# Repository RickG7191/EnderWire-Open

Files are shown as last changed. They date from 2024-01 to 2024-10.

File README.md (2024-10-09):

# EnderWire-Open
This is another option for converting an Ender 3 Pro to a Voron Switchwire. Inspiration for this conversion came from the excellent work of others including [DaRk_dOg](https://github.com/boubounokefalos/Ender_SW/tree/main) and [Steve](https://github.com/stvptrsn).  
  
It is hoped that the 3D printing community will find some value in this work.
  
## Description
One of the key differences that sets this conversion apart from others is that it provides full use of the stock Ender 3 bed size (235x235). The cost of getting that little extra amount involves replacing the top and bottom frame cross members as well as the gantry extrusion with longer versions. One of the replaced 2020 extrusions can be reused as a forward cross member providing better support for the 4040 Y-Axis extrusion, thus it doesn't teeter on the single cross member making frame alignment a bit easier.  

### No Enclosure
This version of the conversion is called "EnderWire-Open" because it does <ins>not</ins> include provisions for an enclosure. For those wanting to print mostly PLA, this is fine as it offers a smaller footprint when not in use. Adaptation to an enclosed version is feasible using longer frame extensions and stretching the side skirts, however I have not endeavored to do so.

### Features
Features of this conversion include:
- Build volume of 235 x 235 x 210
- Optional 6mm or 9mm Y-belt
- Optional smooth idlers or toothed idlers for XY belts
- Optional left endstop, right endstop, or no endstop X-carriage
- XY motor mounts, idler blocks, and gantry blocks optimized for v-slot extrusion
- Shorter Clockwork 2 cable chain mount
- Front skirt option for Mini12864 display or no display
- Front skirt option for hexagon mesh
- Front skirt option to illuminate endcaps with Neopixels or use colored inlay
- Back skirt case fan mount that doesn't use tape (requires gluing 4 small tabs to skirt frame)
- Back skirt standard keystone jacks
- Optional servo actuated Z-probe dock with optional position sensor switches, deck mounted

### Advanced Builder Features
For advanced builders, the following optional features are available:
- Below deck Key-Bak assembly with tension adjustment - [Key-Bak Details](Key-Bak-Details.md)
- Lightened stock bed plate plus alternate Y-carriage
- Custom Z-endstop switch and bracket
- See Build Notes below.

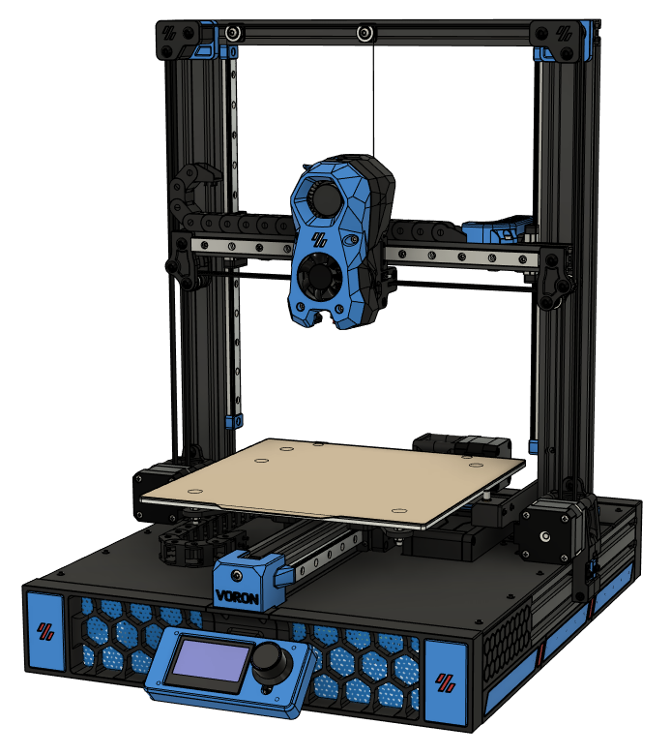
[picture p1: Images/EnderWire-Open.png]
EnderWire Open

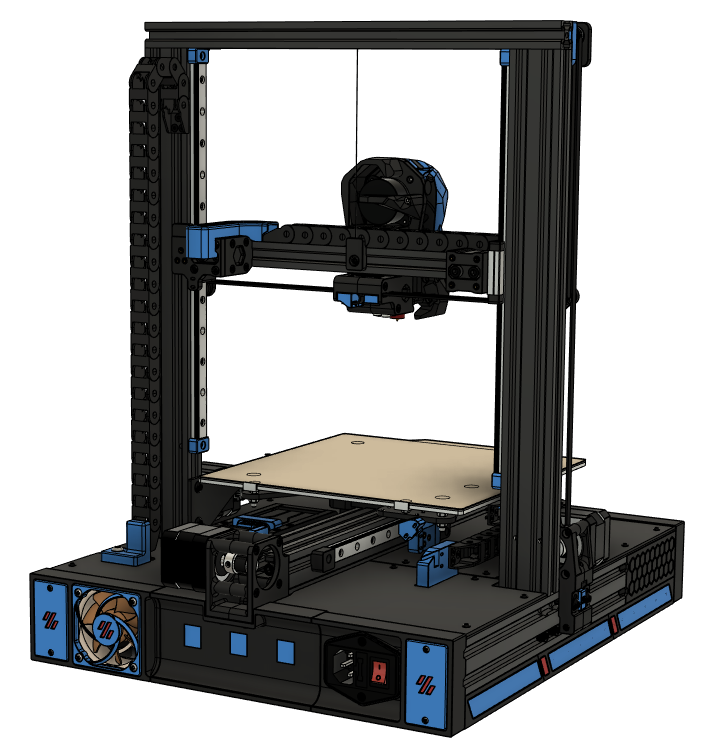
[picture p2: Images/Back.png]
Back View


## Files

### CAD
Complete Fusion 360 files are included in the initial release. Beware, there a upwards of 100 files in the Fusion 360 Archive (.f3z).  
A complete STEP file is included in the CAD folder.

### STLs
STL files for all components except Stealthburner and Mini12864 are included ini the STL folder.

## Bill of Materials
[BOM by Component](BOM-By-Component.md)

## Build Notes
- See [Frame and Gantry Details](Frame-Gantry-Details.md) for information on frame alterations plus gantry idler and belt details.
- The feet are from [Amazon](https://www.amazon.com/gp/product/B00S47D52G/ref=ppx_yo_dt_b_search_asin_title?ie=UTF8&psc=1)
- The Key-Bak assembly uses the spring and 36" Kevlar cord from the regular [13oz Key-Bak](https://www.amazon.com/dp/B0088MQA10?psc=1&ref=ppx_yo2ov_dt_b_product_details)
- The servo used for the Z-probe dock is a TowerPro MG92B from [Adafruit](https://www.adafruit.com/product/2307). I believe an MG90s will also work.
- A modified version of the PCB Klicky probe body and dock are used. The probe has a guard plate that assists with clean docking. The guard plate fits 0.25in x 0.125in countersunk magnets rather than the spec 6mm x 3mm. This is the size I recieved with the kits I purchased. The guard just press fits around the magnets. Glue may be needed.
- The custom z-endstop currently requires a custom PCB to mount the microswitch. Additionally, the support arm for the z-endstop is fabricated from 3mm FR4 / G10 for stiffness.

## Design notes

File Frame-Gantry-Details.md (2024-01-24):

# Frame and Gantry Details
## Frame and Gantry Alteration and Assembly Details
Alterations of the stock Ender 3 Pro frame and gantry includes:
- Replace 2020 Top Cross Member with new 2020 × 360mm v-slot extrusion
- Replace 4040 Main Cross Member with new 2040 × 280mm v-slot extrusion
- Replace 2020 Gantry with new 2020 × 340mm v-slot extrusion
- Repurpose existing 2020 gantry extrusion as new Forward Cross Member
- Add 40×40×13mm Main Bed Beam Spacer and 20×40×13mm Forward Bed Beam Spacer
- Shift 4040 Bed Beam extrusion 20mm forward

The following frame members are used as-is, with the exception of some drilling and tapping as necessary:
- Left & Right Base Members
- Left & Right Columns
- Bed Beam

Reference [Frame Parts](/Images/Frame-Gantry-Details/Frame-Parts.png) for identification of each frame member.  
Reference [Frame Alterations](/Images/Frame-Gantry-Details/Frame-Alterations.png) for overview of new and modified frame members.  

### Bed Beam Spacers
The Main and Forward Bed Beam Spacers may be cut from unused 4040 and 2040 extrusion respectively. Accurate formation of these parts is important for frame squaring and alignment. Since these are very short pieces to work with, and perhaps somewhat difficult to make, STLs for [Printed Spacers](STL/Frame) are an option.

### Required Drilling & Tapping
Aside from cutting new and repurposed extrusions to length, drilling and tapping is required. Specifically, the following is required. Consider laying out and double checking all dimensions for all members prior to performing any cutting or drilling. The instructions below should be accurate, but things happen. Case in point, the Initial Release of the CAD files (Fusion 360) has an error in the location of the tapped holes for the Forward Bed Beam Spacer.
- New 4040 Main Cross Member
  - Tap two holes on each end with an M5×0.8 tap to connect the Left & Right Base Members with 2-M5 SHCS each side
  - Drill four 5.5mm holes midway along the extrusion for 4-M5 SHCS to attach Bed Beam
  - These holes will be 130mm from each end of the extrusion and separated by 20mm at the midpoint
  - Provide clearance for the M5 SHCS heads in the same way as the stock extrusions (a 9mm drill bit should work)
- New 2020 Top Cross Member
  - Drill two 5.5mm holes at each end to align with tapped holes in Left & Right Column Members (10mm and 30mm from ends)
  - The stock Ender 3 Top Cross Member may be used as a template for drilling
  - Provide clearance for the M5 SHCS heads
  - The new Top Cross Member should look just like the stock one, except longer
- New 2020 Forward Cross Member (repurposed 2020 gantry extrusion)
  - Drill one 5.5mm hole 10mm from each end to align with the lower inside holes of the Left & Right Base Members
  - These holes will be 300mm apart along the 320mm long extrusion
  - Drill two 5.5mm holes midway along the extrusion for 2-M5 SHCS to attach the Bed Beam
  - These holes will be 150mm from each of the extrusion and separated by 20mm at the midpoint
  - Provide clearance for the M5 SHCS heads
- Existing Bed Beam Member
  - Confirm that the extrusion is 350mm in length
  - Locate the four existing tapped holes for mounting the Bed Beam to the existing Main Cross Member
  - Drill two 4.2mm holes spaced 20mm backward of the existing holes (105mm from the back end of the extrusion)
  - Drill two 4.2mm holes spaced 80mm from the front end of the extrusion
  - Tap the four new holes with an M5×0.8 tap
  - Ensure that the lower two holes at the front end of the extrusion are tapped for an M5 bolt to attach the Y-Idler
  - Ensure that the four holes at the back end of the extrusion are tapped for an M5 bolt to attach the Y-Motor
- Main and Forward Bed Beam Spacers
  - If using 4040 and 2040 extrusion for bed beam spacers, drill each hole with a 5.5mm drill to provide clearance for M5 bolts
- Existing Left & Right Base Members
  - Ensure that the ends are tapped for M5 bolts to attach the Forward Cross Member and skirt components
- Gantry
  - Aside from cutting the new 2020 Gantry to length, no drilling or tapping is necessary

### Frame Assembly
Assemble the frame using M5×25 and M5×45 SHCS bolts with washers. With the exception of perhaps two M5×25 bolts for the Forward Cross Member, these bolts come from the Ender 3 Pro frame. Refer to the CAD models for specifics. Square and align the frame in the same manner as other builds described elsewhere.

## Gantry, Idler, and Belt Details
### Gantry
The new longer gantry extrusion provides full use of the MGN12 × 300mm linear rail and thus full use of the 235mm bed width and then some. Two options are provided for the gantry belt idlers: toothed or smooth. The smooth idler option is generally more economical as the Gates GT2 toothed idlers can be pricey. Whichever option is chosen for the gantry, the corresponding option should be used for the upper idlers to maintain belt alignment.

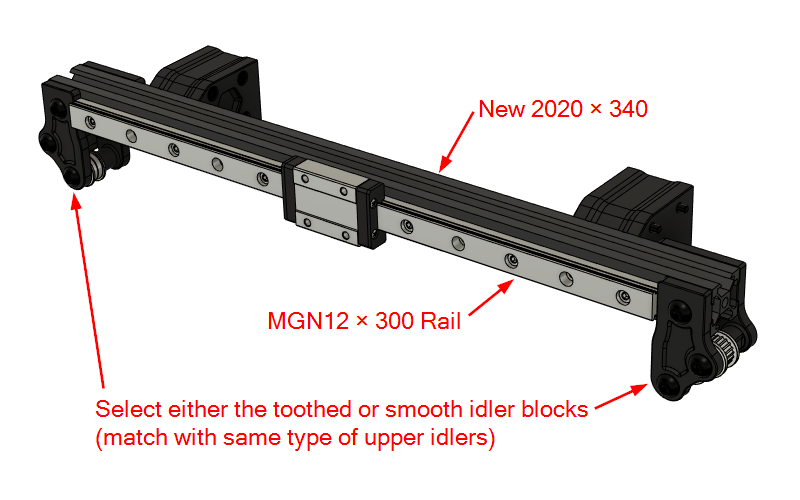
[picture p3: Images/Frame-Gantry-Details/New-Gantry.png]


### Toothed Option
The toothed option requires a total of six toothed idlers, two for the gantry and four for the upper idlers, plus two smooth F695 idler assemblies.

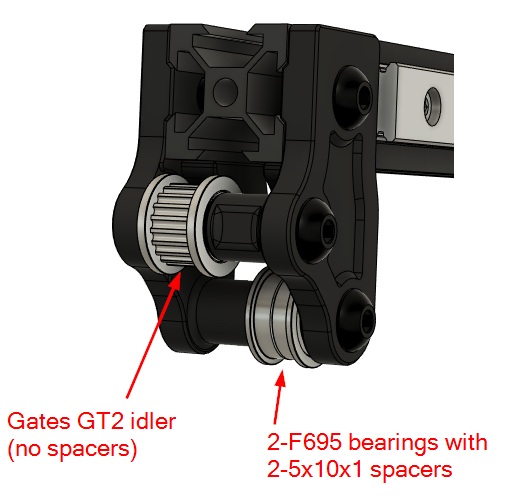
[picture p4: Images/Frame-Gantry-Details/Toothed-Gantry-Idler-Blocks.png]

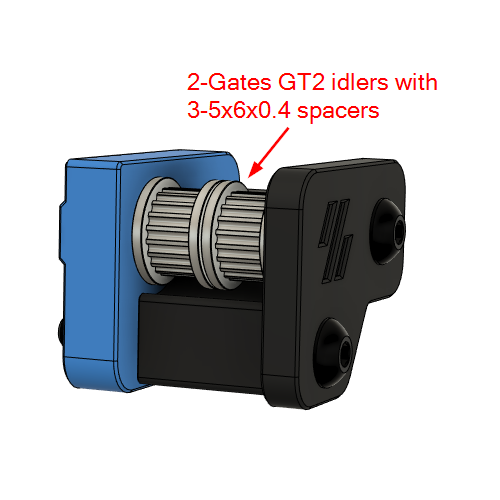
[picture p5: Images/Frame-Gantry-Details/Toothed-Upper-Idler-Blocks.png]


### Smooth Option
The smooth option requires a total of eight F695 idler assemblies.

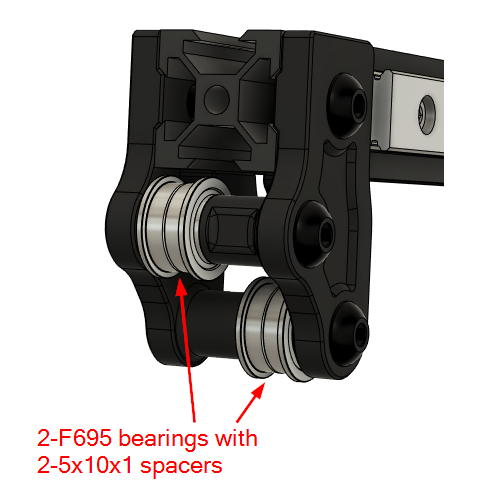
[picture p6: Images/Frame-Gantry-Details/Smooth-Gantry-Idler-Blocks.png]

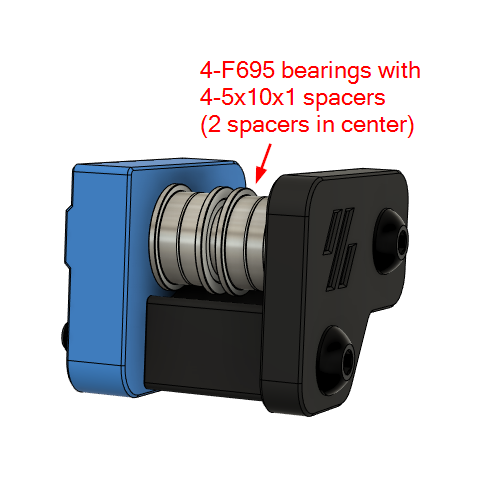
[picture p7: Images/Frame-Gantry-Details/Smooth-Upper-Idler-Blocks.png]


### Belt Details
The Gantry uses Gates 6mm GT2 belting. The spacing and offsets for the XZ belts are identical to Voron Switchwire and the implementation by [DaRk_dOg](https://github.com/boubounokefalos/Ender_SW/tree/main).  
- Belt spacing is 10mm centerline to centerline.
- Centerline of Belt B is 24mm from face of frame.
- Centerline of Belt A is 14mm from face of frame.
- Motor B and Motor A pulley offsets measured from the outside edge of the frame is 10.62mm.

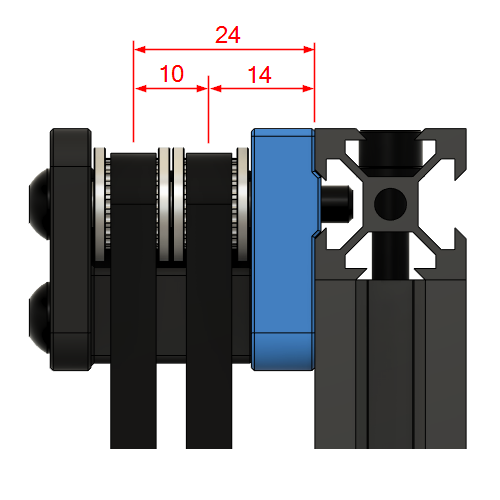
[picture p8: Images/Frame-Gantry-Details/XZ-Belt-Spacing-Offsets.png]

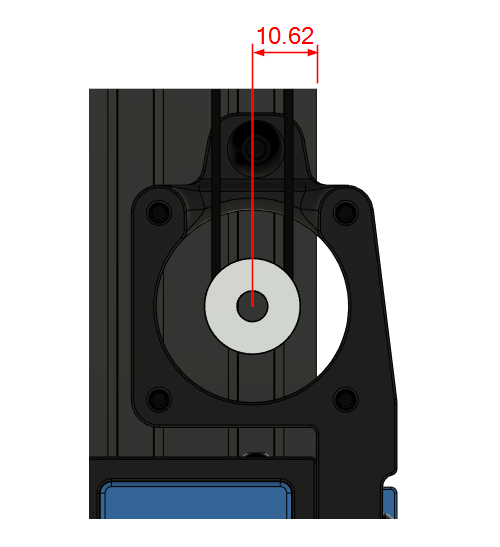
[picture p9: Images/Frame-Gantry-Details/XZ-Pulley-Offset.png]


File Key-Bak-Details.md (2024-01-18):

# Key-Bak Details
The adjustable tension Key-Bak dispenses with the Key-Bak housing and only uses the cord and flat coil spring. As illustrated in the images below, the spring housing meshes with the cord spool in such a way that allows the spring to be wound tighter or looser in order to match the gantry load. In addition to the original intent of the Key-Bak to prevent the grantry from unexpectedly dropping if the XY-motors loose power, it also counterbalances the gantry weight to minimize the differential motor load between upward and downward gantry movements. Note that this sort of adjustment can be accomplished with the unmodified Key-Bak by adjusting the length of the cord. Otherwise, I just wanted the Key-Bak mechanism tucked away under the deck with an easy way to adjust the tension. Personal preference.
## Cord Spool
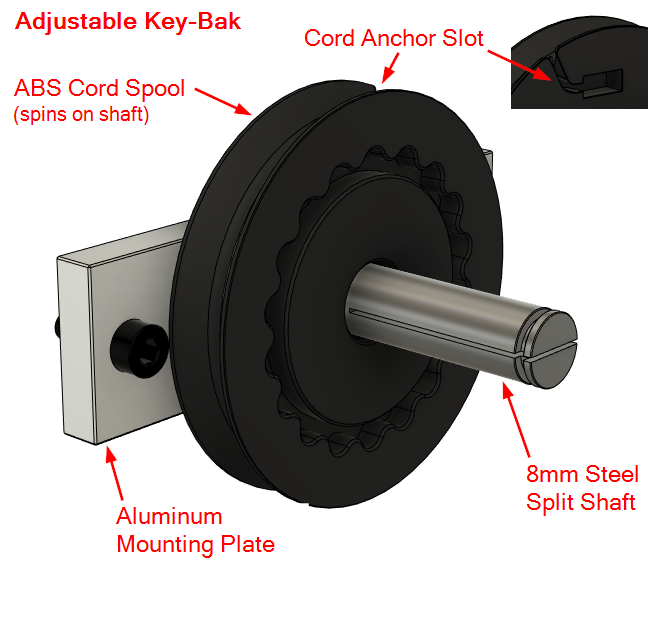
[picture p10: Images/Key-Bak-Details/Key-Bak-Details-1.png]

## Spring Housing
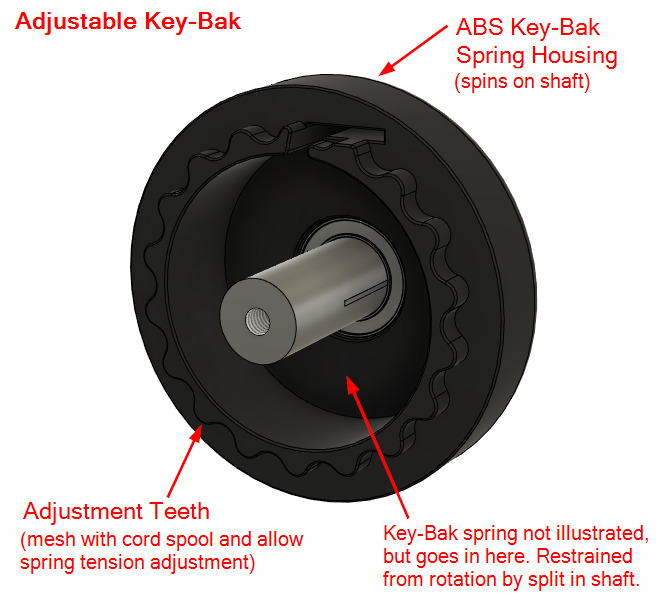
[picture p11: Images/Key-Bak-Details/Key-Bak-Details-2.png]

## Assembled
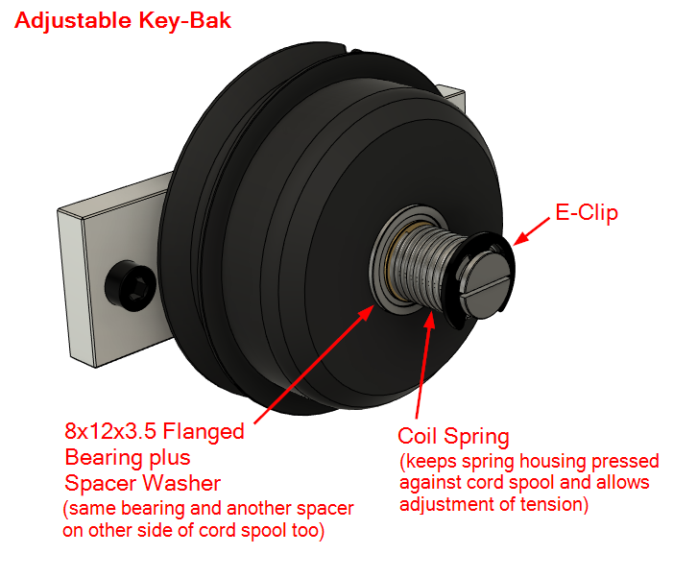
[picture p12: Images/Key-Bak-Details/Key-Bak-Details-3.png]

## Installed
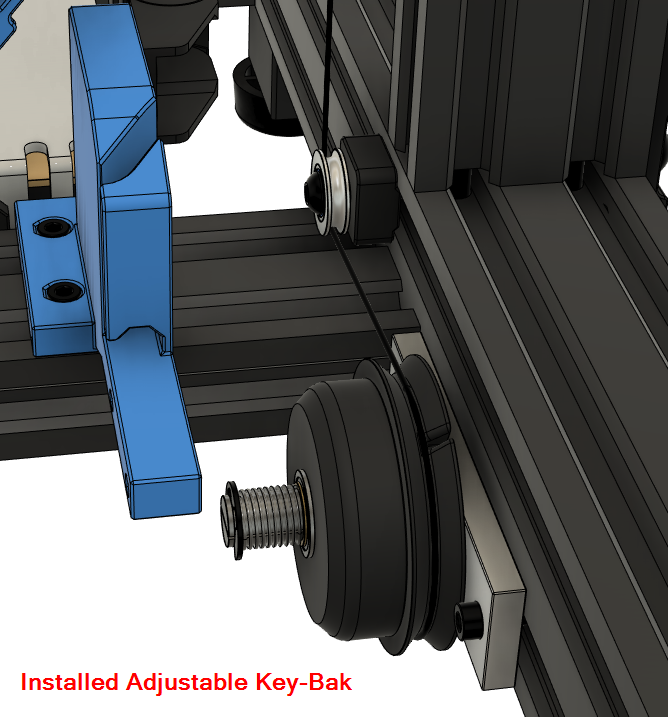
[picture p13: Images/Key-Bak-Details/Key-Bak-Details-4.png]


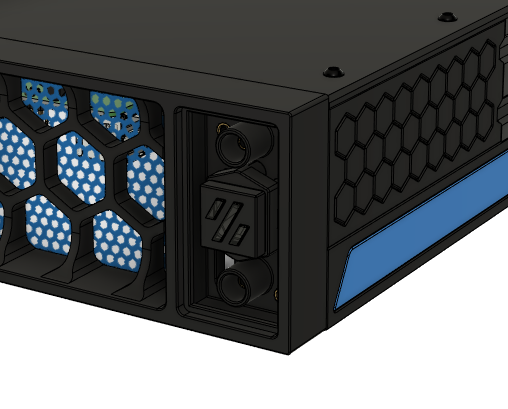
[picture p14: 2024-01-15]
Images/FrontEndcap-Neopixel2.png

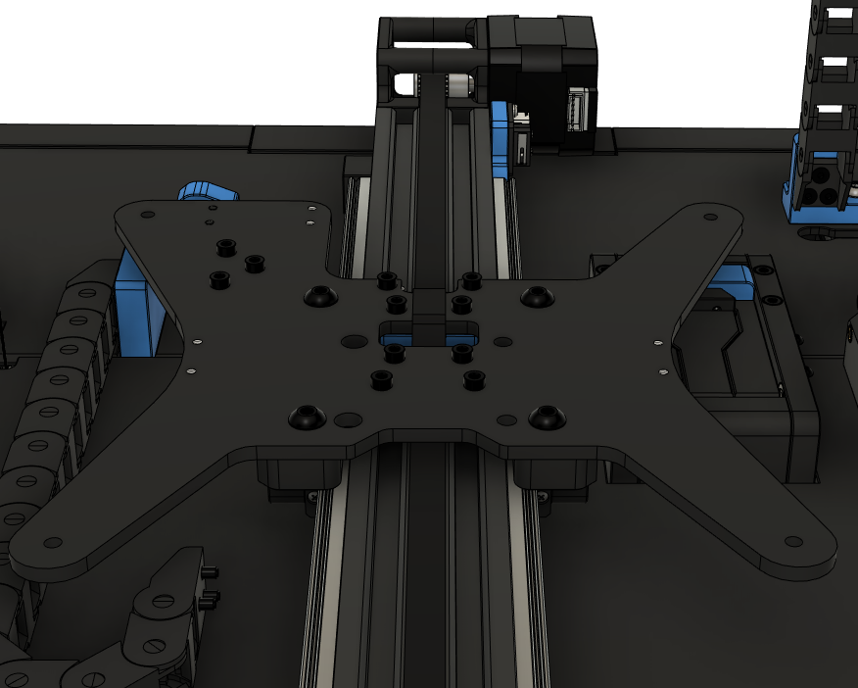
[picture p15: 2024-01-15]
Images/BedPlate.png

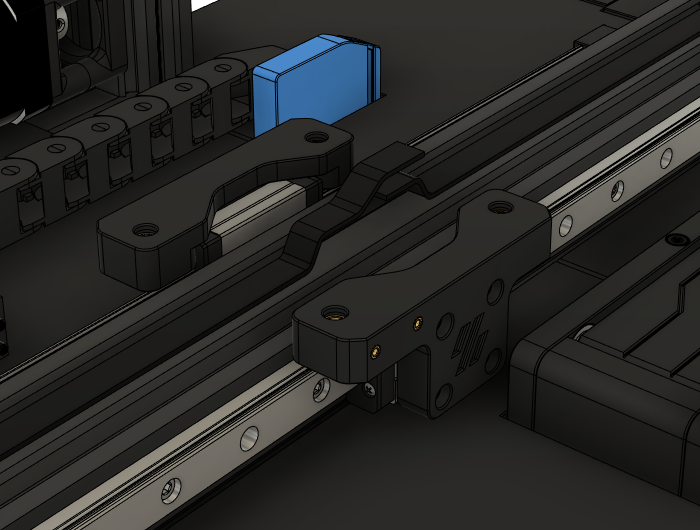
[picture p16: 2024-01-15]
Images/BedCarriage.png

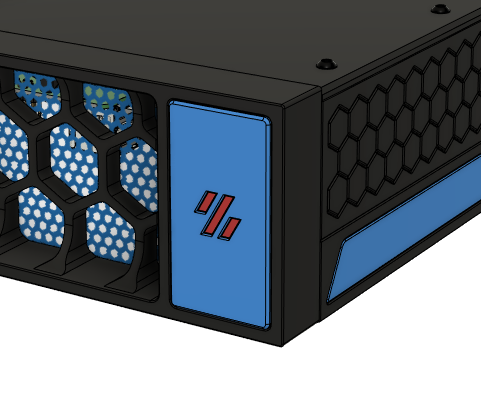
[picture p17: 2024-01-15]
Images/FrontEndcap-Inlay.png

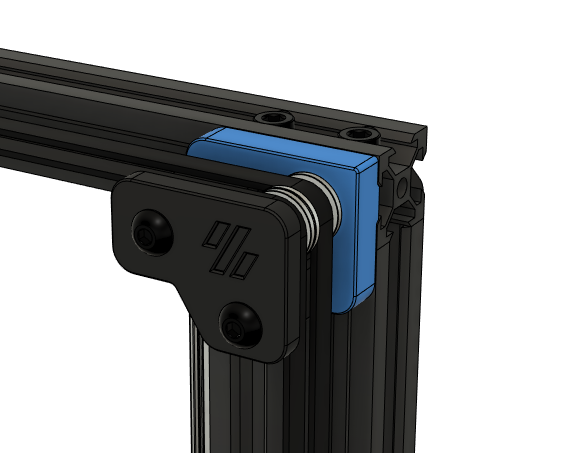
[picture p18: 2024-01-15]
Images/UpperIdlerToothed.png

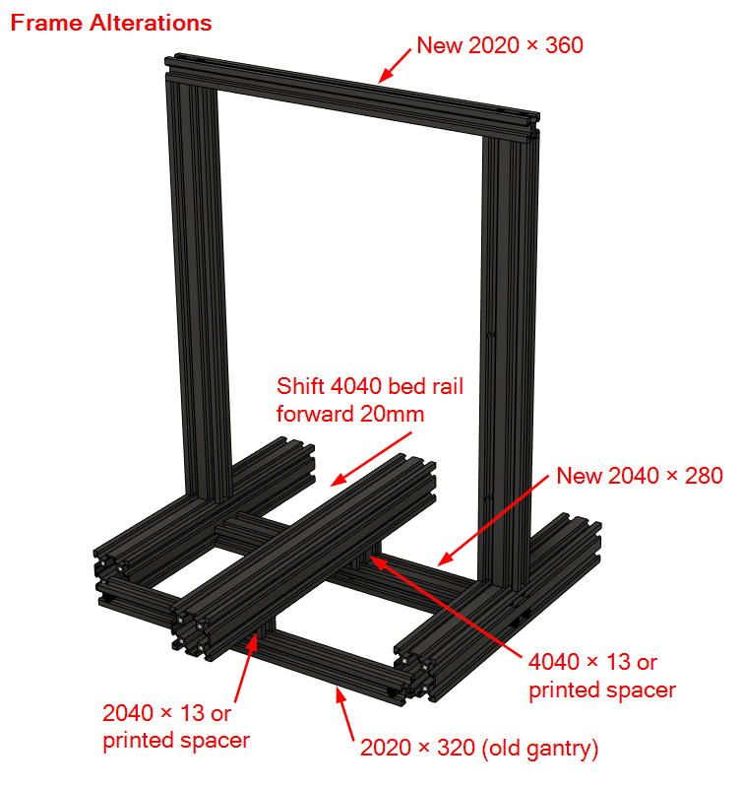
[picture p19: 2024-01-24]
Images/Frame-Gantry-Details/Frame-Alterations.png

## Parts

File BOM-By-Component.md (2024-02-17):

# BOM By Component
Parts and hardware broken down by component. See CAD files for specific details.
<br/><br/>
Items currently not included in this listing:
- Stealthburner toolhead
- Mini12864 display
- Z-Endstop (this currently requires a fiberglass bracket and custom PCB)
- Below deck Key-Bak (this currently requires machined pulleys, machined pin, and aluminum mounting plate)
<br/><br/>

| Component | Count | Part Description | Note |
| :--- | :---: | :--- | :--- |
| Frame | 1 | 2020 × 340 V-Slot Extrusion | Gantry |
| Frame | 1 | 2020 × 360 V-Slot Extrusion | Top Cross Member |
| Frame | 1 | 2040 × 280 V-Slot Extrusion | Main Cross Member |
| Frame | 14 | M5 × 45 SHCS | w/washer |
| Frame | 6 | M5 × 25 SHCS | w/washer |
||
| Linear Rails | 5 | MGN12 × 300 | |
| Linear Rails | 30 | M3 × 8 SHCS | 6 each rail |
| Linear Rails | 30 | M3 T-Nut | 6 each rail |
||
| XZ-Motor Mounts | 2 | 6mm GT2 20T Pulley | |
| XZ-Motor Mounts | 4 | M3 Threaded Insert | |
| XZ-Motor Mounts | 10 | M3 × 30 SHCS | |
| XZ-Motor Mounts | 2 | M3 × 40 SHCS | |
| XZ-Motor Mounts | 2 | M5 × 10 BHCS | |
| XZ-Motor Mounts | 4 | M5 × 16 BHCS | |
| XZ-Motor Mounts | 6 | M5 T-Nut | |
||
| Y-Motor Mount - 9mm Option | 1 | 9mm GT2 20T Pulley | |
| Y-Motor Mount - 9mm Option | 3 | M3 Threaded Insert | |
| Y-Motor Mount - 9mm Option | 1 | M3 × 35 SHCS | |
| Y-Motor Mount - 9mm Option | 4 | M3 × 40 SHCS | |
| Y-Motor Mount - 9mm Option | 2 | M5 × 16 SHCS | |
| Y-Motor Mount - 9mm Option | 2 | M5 × 16 BHCS | |
||
| Y-Motor Mount - 6mm Option | 1 | 6mm GT2 20T Pulley | |
| Y-Motor Mount - 6mm Option | 3 | M3 Threaded Insert | |
| Y-Motor Mount - 6mm Option | 1 | M3 × 35 SHCS | |
| Y-Motor Mount - 6mm Option | 4 | M3 × 40 SHCS | |
| Y-Motor Mount - 6mm Option | 4 | M5 × 16 BHCS | |
||
| Y-Idler - 9mm Option | 1 | 9mm GT2 20T Idler | |
| Y-Idler - 9mm Option | 1 | 5 × 24 Pin | |
| Y-Idler - 9mm Option | 2 | 5 × 7 × 0.5 Spacer | |
| Y-Idler - 9mm Option | 2 | M3 Threaded Insert | |
| Y-Idler - 9mm Option | 1 | M4 Threaded Insert | |
| Y-Idler - 9mm Option | 1 | M4 × 12 BHCS | |
| Y-Idler - 9mm Option | 2 | M5 × 16 BHCS | |
||
| Y-Idler - 6mm Option | 1 | 6mm GT2 20T Idler | |
| Y-Idler - 6mm Option | 1 | 5 × 20 Pin | |
| Y-Idler - 6mm Option | 2 | 5 × 7 × 0.5 Spacer | |
| Y-Idler - 6mm Option | 2 | M3 Threaded Insert | |
| Y-Idler - 6mm Option | 1 | M4 Threaded Insert | |
| Y-Idler - 6mm Option | 1 | M4 × 12 BHCS | |
| Y-Idler - 6mm Option | 2 | M5 × 16 BHCS | |
||
| Bed Carriage | 2 | M2 Threaded Insert | For ADXL |
| Bed Carriage | 4 | M5 Threaded Insert | |
| Bed Carriage | 8 | M3 × 8 SHCS | |
| Bed Carriage | 4 | M5 × 16 BHCS | |
||
| Y-Belt Clamp | 8 | M3 Threaded Insert | |
| Y-Belt Clamp | 8 | M3 × 12 SHCS | |
||
| Y-Chain Mount - Bed | 6 | M3 Threaded Insert | |
| Y-Chain Mount - Bed | 3 | M3 × 12 SHCS | |
| Y-Chain Mount - Bed | 3 | M3 × 6 FHCS | |
| Y-Cable Mount - Bed | 2 | M3 × 8 SHCS | |
||
| Y-Chain Mount - Base | 3 | M3 Threaded Insert | |
| Y-Chain Mount - Base | 2 | M3 × 8 SHCS | |
| Y-Chain Mount - Base | 2 | M3 T-Nut | |
| Y-Chain Mount - Base | 3 | M3 × 6 FHCS | |
||
| Y-Limit Switch | 1 | Creality Endstop PCB | |
| Y-Limit Switch | 2 | M2.5 × 6 STS | |
| Y-Limit Switch | 2 | M3 × 8 SHCS | |
| Y-Limit Switch | 2 | M3 T-Nut | |
||
| Y-Carriage Stop | 1 | M3 × 8 SHCS | |
| Y-Carriage Stop | 1 | M3 T-Nut | |
||
| Z-Carriage Stops | 4 | M3 × 8 SHCS | |
| Z-Carriage Stops | 4 | M3 T-Nut | |
||
| Z-Bearing Blocks | 8 | M3 Threaded Insert | |
| Z-Bearing Blocks | 8 | M3 × 30 SHCS | |
| Z-Bearing Blocks | 4 | M5 × 40 SHCS | |
| Z-Bearing Blocks | 4 | M5 T-Nut | |
||
| Gantry Pulley Blocks - Toothed Option | 2 | 6mm GT2 20T Idler | |
| Gantry Pulley Blocks - Toothed Option | 4 | F695 Bearing | |
| Gantry Pulley Blocks - Toothed Option | 4 | 5 × 10 × 1 Spacer | |
| Gantry Pulley Blocks - Toothed Option | 6 | M5 × 10 BHCS | |
| Gantry Pulley Blocks - Toothed Option | 4 | M5 × 30 BHCS | |
| Gantry Pulley Blocks - Toothed Option | 6 | M5 T-Nut | |
||
| Gantry Pulley Blocks - Smooth Option  | 8 | F695 Bearing | |
| Gantry Pulley Blocks - Smooth Option  | 8 | 5 × 10 × 1 Spacer | |
| Gantry Pulley Blocks - Smooth Option  | 6 | M5 × 10 BHCS | |
| Gantry Pulley Blocks - Smooth Option  | 4 | M5 × 30 BHCS | |
| Gantry Pulley Blocks - Smooth Option  | 6 | M5 T-Nut | |
||
| Upper Idlers - Toothed Option | 4 | 6mm GT2 20T Idler | |
| Upper Idlers - Toothed Option | 2 | 5 × 30 Pin | |
| Upper Idlers - Toothed Option | 6 | 5 × 6 × 0.4 Spacer | |
| Upper Idlers - Toothed Option | 4 | M5 × 40 BHCS | |
| Upper Idlers - Toothed Option | 4 | M5 T-Nut | |
||
| Upper Idlers - Smooth Option | 8 | F695 Bearing | |
| Upper Idlers - Smooth Option | 2 | 5 × 30 Pin | |
| Upper Idlers - Smooth Option | 8 | 5 × 10 × 1 Spacer | |
| Upper Idlers - Smooth Option | 4 | M5 × 40 BHCS | |
| Upper Idlers - Smooth Option | 4 | M5 T-Nut | |
||
| X-Carriage | 12 | M3 Threaded Insert | |
| X-Carriage | 4 | M3 × 8 SHCS | |
| X-Carriage | 6 | M3 × 12 SHCS | |
| X-Carriage | 2 | M3 × 16 SHCS | |
| X-Carriage | 3 | M3 × 40 SHCS | |
| X-Carriage | 3 | M3 Hex Nut | |
| X-Carriage | 1 | Omron D2F-L Switch | Optional X-Endstop  |
| X-Carriage | 2 | M2 × 10 STS | Optional X-Endstop  |
||
| Z-Chain Mount - Gantry | 3 | M3 Threaded Insert | |
| Z-Chain Mount - Gantry | 4 | M3 × 8 BHCS | |
| Z-Chain Mount - Gantry | 3 | M3 × 6 FHCS | |
||
| Z-Chain Mount - Base | 3 | M3 Threaded Insert | |
| Z-Chain Mount - Base | 3 | M3 × 6 FHCS | |
| Z-Chain Mount - Base | 1 | M5 × 16 BHCS | |
| Z-Chain Mount - Base | 1 | M5 T-Nut | |
||
| XZ-Cable Cover | 1 | M3 × 8 SHCS | |
| XZ-Cable Cover | 1 | M3 T-Nut | |
||
| Foot Risers | 4 | M5 × 16 BHCS | |
| Foot Risers | 4 | M5 × 20 BHCS | |
| Foot Risers | 4 | M5 Hex Nut | |
||
| Bottom Panel | 1 | 3 × 352 × 398 Acrylic Panel | |
| Bottom Panel | 4 | M3 × 8 BHCS | |
||
| Bottom Panel Support Brackets | 2 | M3 Threaded Insert | |
| Bottom Panel Support Brackets | 4 | M2 × 10 STS | |
||
| Frame Extensions | 8 | M3 Threaded Insert | |
| Frame Extensions | 8 | M3 × 8 SHCS | |
| Frame Extensions | 4 | M5 × 12 BHCS | |
||
| Front Skirt | 14 | M3 Threaded Insert | |
| Front Skirt | 10 | M3 × 8 SHCS | |
| Front Skirt | 2 | M3 × 16 SHCS | Mini12864 mounting  |
||
| Front Skirt Endcaps | 4 | M3 Threaded Insert | |
| Front Skirt Endcaps | 2 | Neopixel | LED option |
||
| Back Skirt | 4 | M2 Threaded Insert | |
| Back Skirt | 9 | M3 Threaded Insert | |
| Back Skirt | 6 | M3 × 8 SHCS | |
| Back Skirt | 8 | M5 × 12 BHCS | |
||
| Back Skirt Endcaps | 4 | M2 × 6 BHCS | |
||
| Power Inlet | 1 | Ender 3 Power Inlet | |
| Power Inlet | 2 | M3 × 10 FHCS | |
||
| Shock Guard | 1 | M3 × 20 SHCS | |
||
| Case Fan | 1 | 60mm Fan | |
| Case Fan | 4 | M3 Threaded Insert | |
| Case Fan | 4 | M3 × 8 BHCS | |
||
| Fan Deflector | 2 | M3 × 8 SHCS | |
| Fan Deflector | 2 | M3 T-Nut | |
||
| Side Skirts | 2 | M3 Threaded Insert | |
| Side Skirts | 22 | M2.5 × 5 STS | |
| Side Skirts | 22 | M3 × 8 SHCS | |
||
| Power Supply Brackets | 4 | M3 × 8 SHCS | |
| Power Supply Brackets | 4 | M3 T-Nut | |
| Power Supply Brackets | 4 | M4 × 6 BHCS | |
||
| Deck Panels | 18 | M3 × 8 BHCS | |
| Deck Panels | 6 | M3 T-Nut | |
||
| Deck Panel Supports | 8 | M3 Threaded Insert | |
| Deck Panel Supports | 4 | M3 × 20 SHCS | |
||
| Y-Cable Cover | 1 | M3 × 8 SHCS | |
| Y-Cable Cover | 1 | M3 T-Nut | |
||
| DIN Rails | 1 | DIN35 × 200mm | Front |
| DIN Rails | 1 | DIN35 × 160mm | Back |
| DIN Rails | 4 | M5 × 6 BHCS | |
| DIN Rails | 4 | M5 T-Nut | |
||
| XZ-Belts | 2 | 6mm GT2 × 1550mm | Includes 50mm extra |
||
| Y Belt - 9mm Option | 1 | 6mm GT2 × 900mm | Includes 50mm extra |
| Y-Belt - 6mm Option | 1 | 9mm GT2 × 900mm | Includes 50mm extra |
||
| Z-Probe Dock | 1 | TowerPro MG92B Servo | |
| Z-Probe Dock | 2 | F695 Bearing | |
| Z-Probe Dock | 1 | 5 × 50 Pin | |
| Z-Probe Dock | 2 | 5 × 10 × 1 Spacer | |
| Z-Probe Dock | 2 | M2 Threaded Insert | |
| Z-Probe Dock | 2 | M2 × 6 SHCS | Servo mounting |
| Z-Probe Dock | 1 | M2 × 8 SHCS | Link rod |
| Z-Probe Dock | 1 | M2 × 12 SHCS | Link rod |
| Z-Probe Dock | 2 | M2 Washer | Link rod |
| Z-Probe Dock | 1 | M2 Hex Nut | Link rod |
| Z-Probe Dock | 2 | 2 × 3.4 × 3.4 Bushing | Link rod |
| Z-Probe Dock | 5 | M3 Threaded Insert | |
| Z-Probe Dock | 3 | M3 × 12 SHCS | |
| Z-Probe Dock | 1 | M3 × 16 SHCS | |
| Z-Probe Dock | 4 | M3 × 45 SHCS | |
| Z-Probe Dock | 1 | M3 Hex Nut | |
| Z-Probe Dock | 4 | M3 T-Nut | |
| Z-Probe Dock | 2 | Omron D2F-L Switch | Optional |
| Z-Probe Dock | 4 | M2 × 10 STS | Optional |
||
| PCB Klicky Dock | 2 | 6 × 3 Magnets | |
| PCB Klicky Dock | 4 | M2 × 8 STS | |
| PCB Klicky Dock | 2 | M3 × 6 FHCS | |

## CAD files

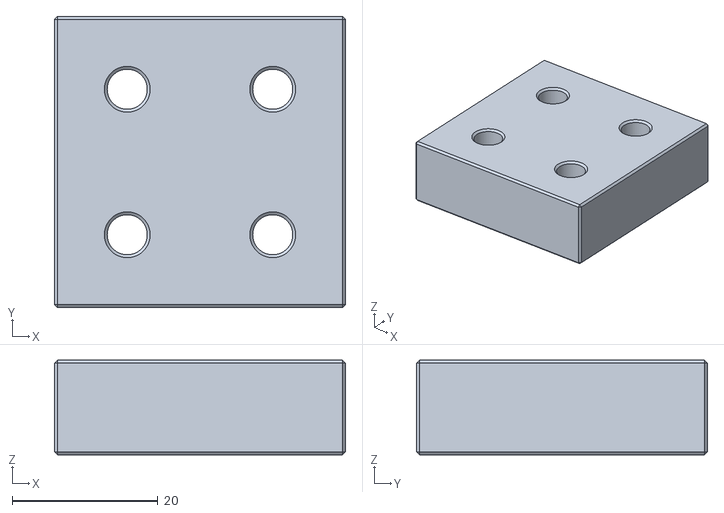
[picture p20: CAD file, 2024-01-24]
STL/Frame/main_bed_beam_spacer.stl
40.0 x 40.0 x 13.0

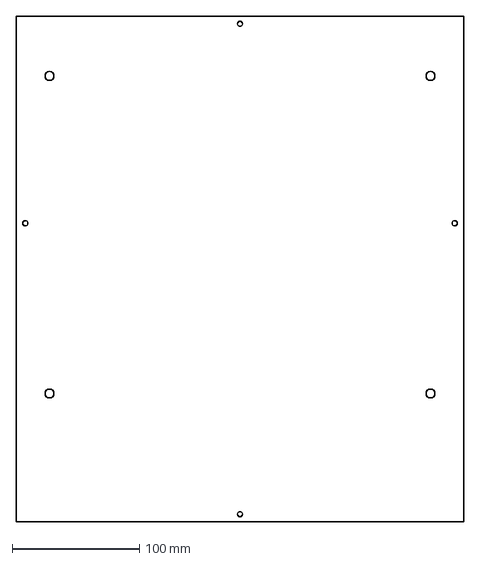
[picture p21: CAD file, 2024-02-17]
DXF/BottomPanel.dxf
352.0 x 398.0 mm

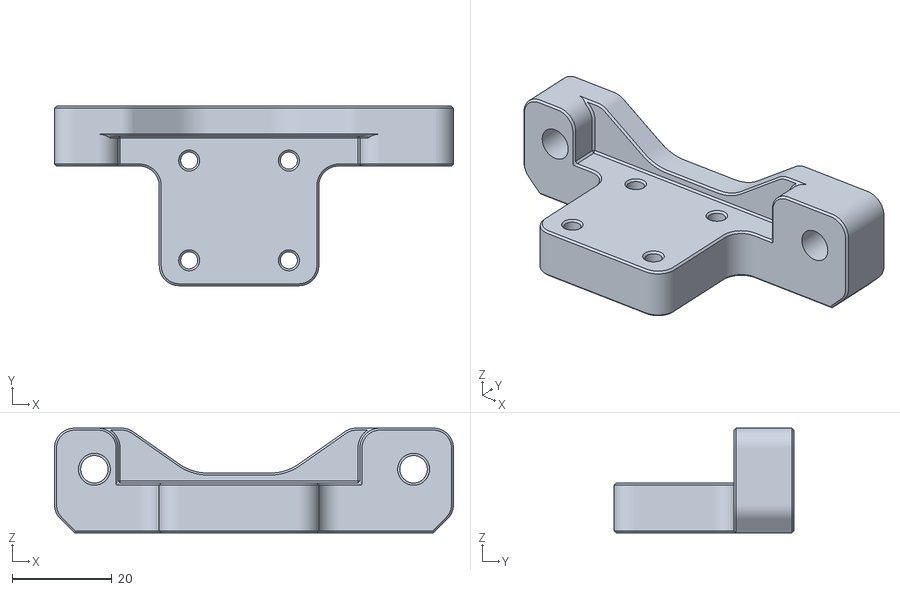
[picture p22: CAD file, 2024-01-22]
STL/Bed/y_axis_bed_carriage_a.stl
80.0 x 36.0 x 21.0

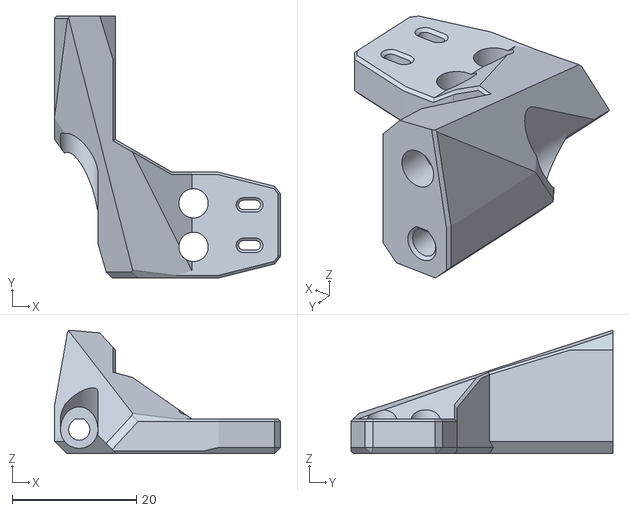
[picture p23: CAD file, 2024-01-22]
STL/Clockwork_2/chain_anchor_3hole_sw_short.stl
36.4 x 42.1 x 19.8

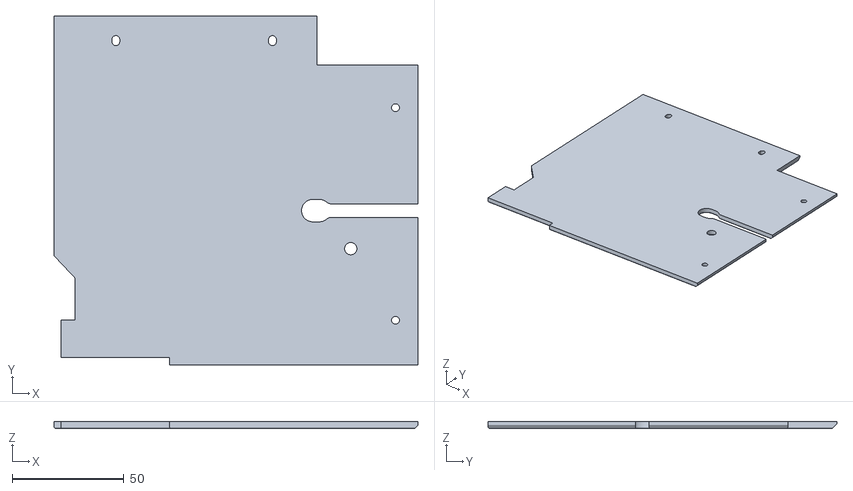
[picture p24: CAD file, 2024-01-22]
STL/Deck/deck_back_right.stl
162.6 x 156.0 x 3.00

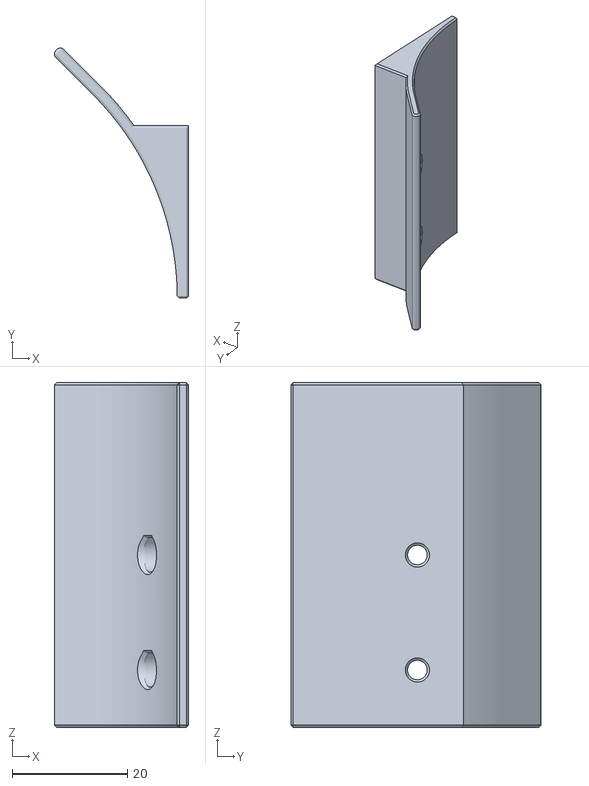
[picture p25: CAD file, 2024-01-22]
STL/Electronics/fan_deflector.stl
23.4 x 43.5 x 60.0

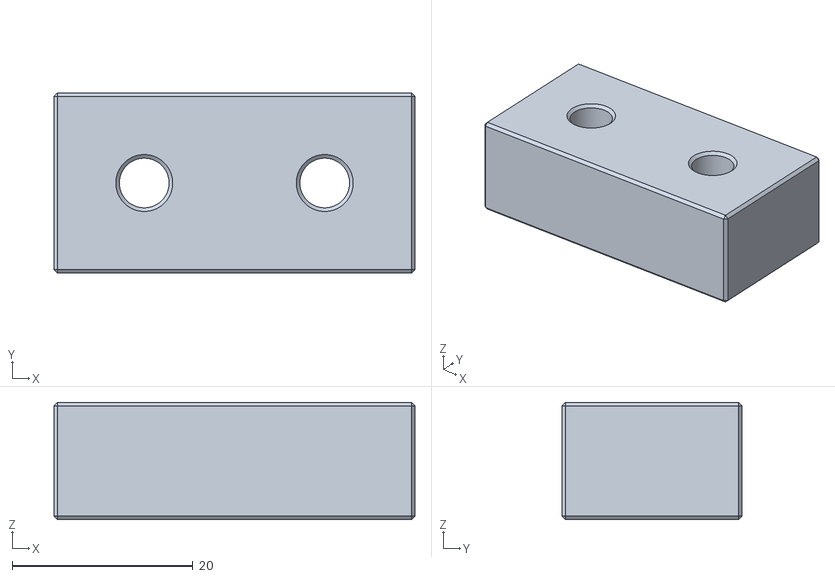
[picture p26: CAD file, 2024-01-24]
STL/Frame/forward_bed_beam_spacer.stl
40.0 x 20.0 x 13.0

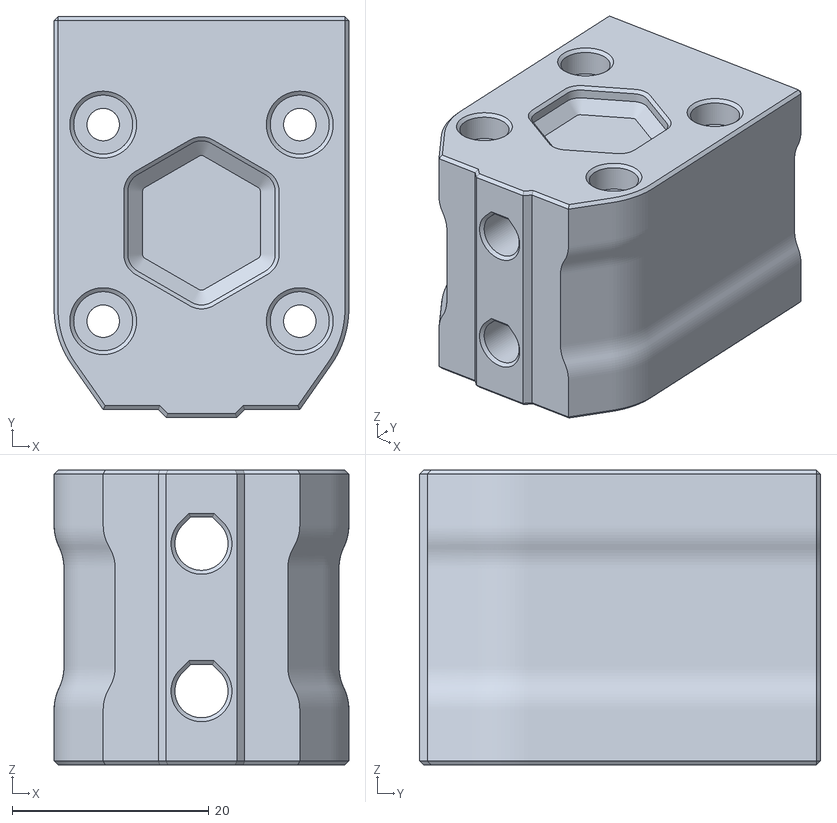
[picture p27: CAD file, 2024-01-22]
STL/Gantry/z_bearing_block_x2.stl
30.0 x 40.8 x 30.0

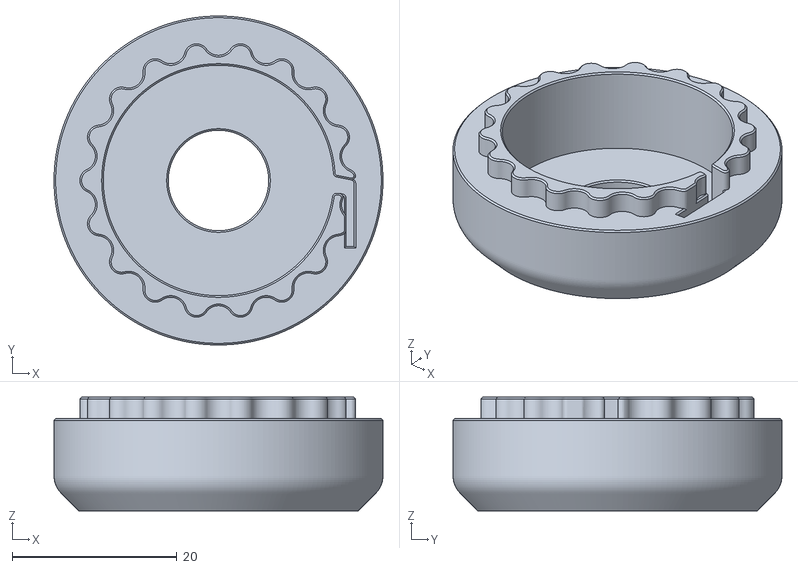
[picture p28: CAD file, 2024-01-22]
STL/KeyBak/keybak_spring_housing.stl
40.0 x 40.0 x 13.8

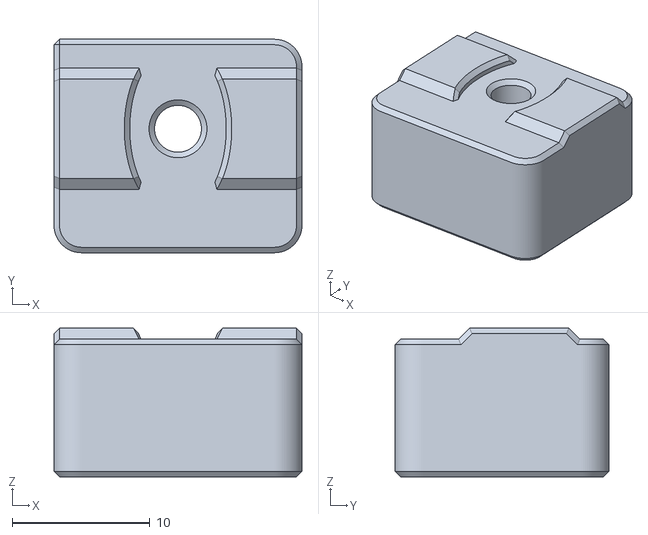
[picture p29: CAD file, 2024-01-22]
STL/Misc/y_carriage_stop.stl
18.0 x 15.5 x 10.8

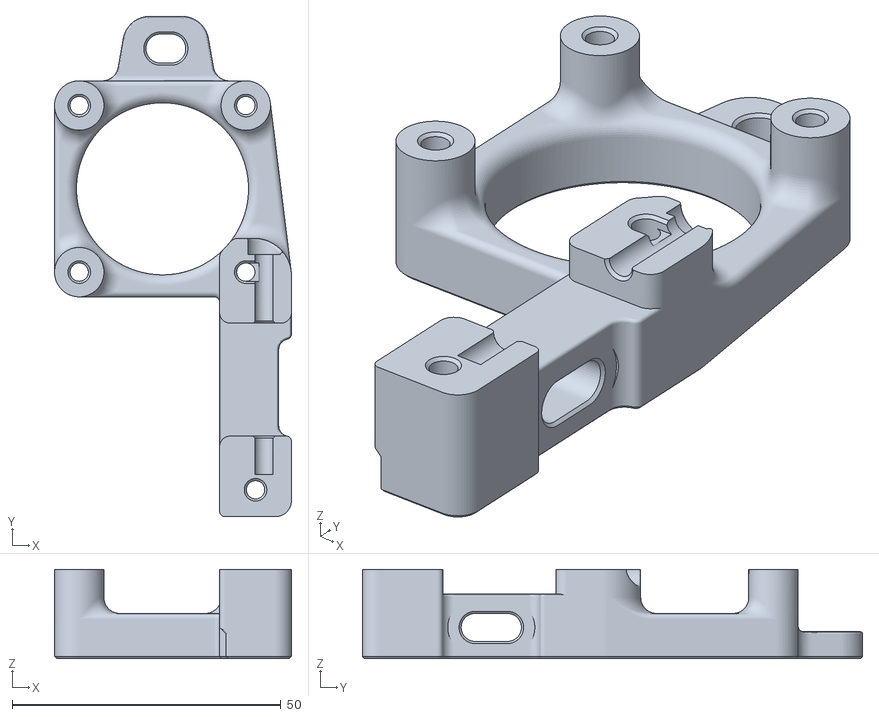
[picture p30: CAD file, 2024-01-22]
STL/Motors/a_motor_mount_b.stl
44.1 x 93.1 x 16.6

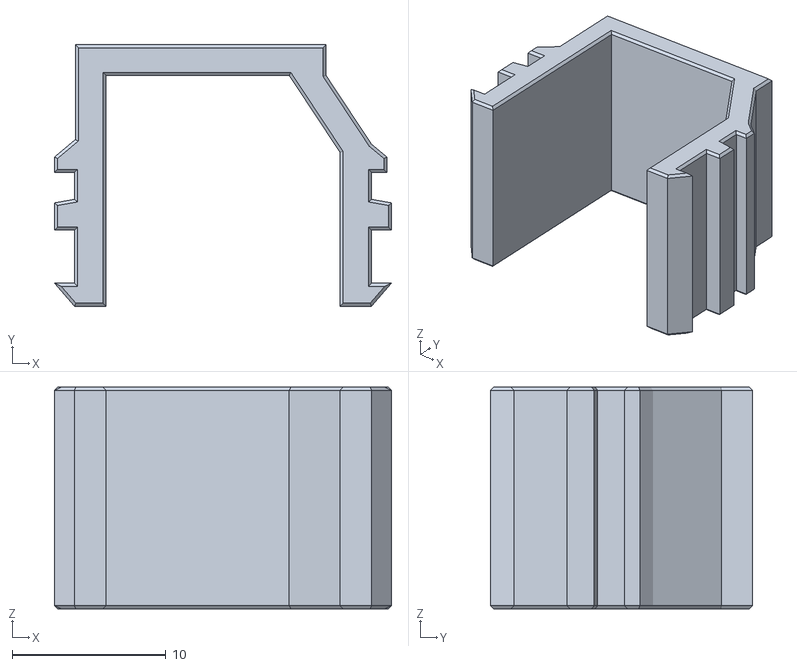
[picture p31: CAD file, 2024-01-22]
STL/Skirt/Back/[a]_keystone_jack_blank.stl
21.9 x 17.0 x 14.4

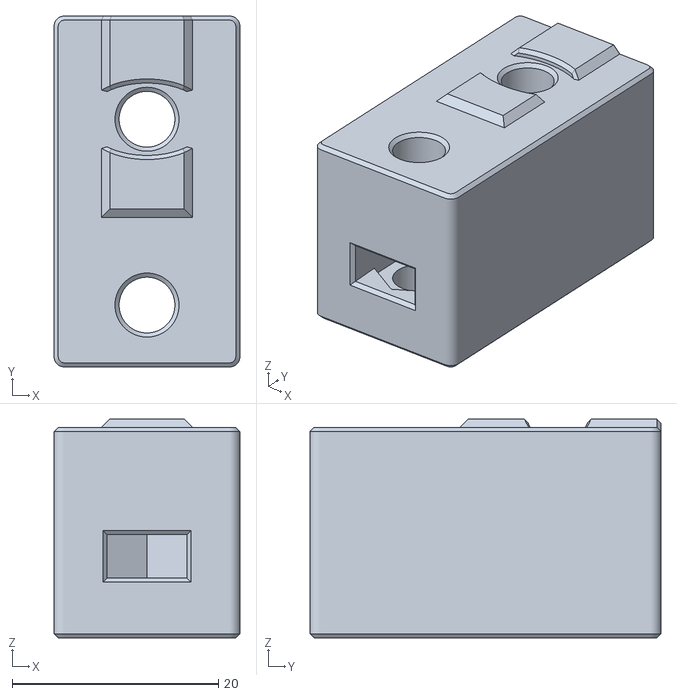
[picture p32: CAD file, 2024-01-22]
STL/Skirt/foot_riser_x4.stl
18.0 x 34.0 x 21.2

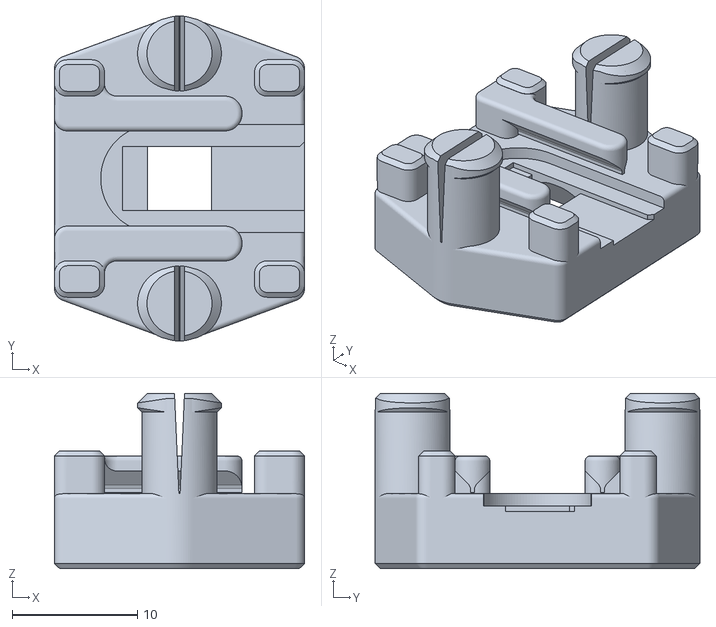
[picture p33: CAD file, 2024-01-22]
STL/Skirt/Front/[o]_led_carrier.stl
20.0 x 26.0 x 14.0

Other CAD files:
STL/Skirt/Sides/[a2]_side_skirt_inlay_right_b_x2.stl
STL/Upper_Idlers/upper_idler_support_toothed_left_b.stl
STL/X_Carriage/[a]_x_carriage_probe_bracket.stl
STL/Y_Idler/[a]_y_belt_tensioner_6mm.stl
DXF/DeckPanels.dxf
DXF/DeckPanelsZ-Probe.dxf
STL/Bed/[a]_y_cable_mount_bed.stl
STL/Bed/[a]_y_chain mount_bed.stl
STL/Bed/[a]_y_clamp_block_x2.stl
STL/Bed/y_axis_bed_carriage_b.stl
STL/Bed/y_clamp_belt_guide.stl
STL/Deck/deck_back_left.stl
STL/Deck/deck_back_right_zprobe.stl
STL/Deck/deck_front_left.stl
STL/Deck/deck_front_right.stl
STL/Deck/deck_front_right_zprobe.stl
STL/Deck/deck_panel_support_x4.stl
STL/Electronics/[a]_y_chain mount_base.stl
STL/Electronics/[a]_y_limit_switch_mount.stl
STL/Electronics/[a]_z_chain_mount_base.stl
STL/Electronics/chain_shim.stl
STL/Electronics/daygreen_dc-dc_mount.stl
STL/Electronics/din_clip_low_profile.stl
STL/Electronics/ldo_breakout_mount_lp.stl
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

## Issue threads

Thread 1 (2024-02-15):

Which BOM should we follow?

Gaetan36, 2024-02-15:
Good morning,
Firstly, thank you for your incredible work, it perfectly meets what I was looking for.
To avoid making mistakes, could you tell me which BOM I should follow please?
Thank you so much

RickG7191, 2024-02-16:
At the moment there isn't a BOM developed for this other than what is documented within the Fusion CAD files. I'll see if I can put something together.

Gaetan36, 2024-02-16:
Alright i understand.
Or maybe i can follow the BOM of https://github.com/walttriano/VoronUsers/tree/master/printer_mods/Triano/Ender_3Pro_Switchwire ?

Gaetan36, 2024-02-16:
Alright, i will see the CAD files then. Thank for your answer

RickG7191, 2024-02-17:
I've added [BOM by Component](https://github.com/RickG7191/EnderWire-Open/blob/main/BOM-By-Component.md).

Closed 2024-02-18.

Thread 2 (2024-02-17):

Deck Panel dxf files

Gaetan36, 2024-02-17:
Good morning,
Is it possible to have the deck panels in one piece (top and bottom) in dxf file please ?
It seems to me that the upper deck must still have two parts.
I would like to have them laser cut from plexiglass to have a clean surface.
I thank you in advance.

RickG7191, 2024-02-17:
Added [DXF](https://github.com/RickG7191/EnderWire-Open/tree/main/DXF) files.

Gaetan36, 2024-02-17:
That's perfect, thank you very much !

Closed 2024-02-18.

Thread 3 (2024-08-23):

CAD file can't be opened?

madorax251, 2024-08-23:
I downloaded the CAD file but there was an error when I opened it

RickG7191, 2024-08-30:
What was the error message?

madorax251, 2024-09-10:
CAD file can't be opened. Can you update the step file so it can be opened
in Fusion?

Pada Jum, 30 Agu 2024 pukul 20.15 Rick G ***@***.***> menulis:

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

RickG7191, 2024-09-22:
Just tested uploading the F3Z file and it works fine. Make sure you "Upload" the file rather than trying to just open it. An F3Z file is just a ZIP file.

ilf-S, 2024-10-08:
Just pitching in. As a Linux user, the only CAD software I know and have access to is FreeCAD. I attempted to install Fusion 360, because some good person created an entire github project for installing Fusion 360 on a variety of Linux distros, but unfortunately, even after installing it and spending few hours to familiarize myself with it, uploading is severely broken. Please be a good person and export it as a step file like all of the Voron projects, don't gatekeep your good work. I want to be able to take a look at your work and find out if I can go with t-slotted alu profiles vs v-slotted, as for v-slots I have to wait few weeks, while I can get t-slots tomorrow.

RickG7191, 2024-10-09:
Thank you for pointing out the Linux issue in not having Fusion 360. I've exported it to step and uploaded to CAD folder. Please let me know if you have any issues with the file. I previously had issues getting the step file to open in Fusion and FreeCAD, but this one appears to be opening fine.

ilf-S, 2024-10-09:
After fighting for another couple of hours with Fusion 360 under wine on Linux, I too managed to export a STEP file. Currently testing yours. Looks good, and I already see what I need to modify for a T-Slot. I have few questions about your build, what would be the appropriate venue to ask them? The voron forum? I don't want to turn github into chat session.

RickG7191, 2024-10-10:
My Discord username is rgreenfield71. Feel free to direct message me.

Closed 2025-01-30.

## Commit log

2024-01-22 Oriented STLs for printing
2024-01-24 Reference to Frame & Gantry Details
2024-02-17 Added BOM by Component
2024-02-17 Added DXF files for deck and bottom panels
    [BottomPanel.dxf, DeckPanels.dxf, DeckPanelsZ-Probe.dxf]
2024-10-09 Update README.md
    Added text regarding STEP file in CAD folder.
